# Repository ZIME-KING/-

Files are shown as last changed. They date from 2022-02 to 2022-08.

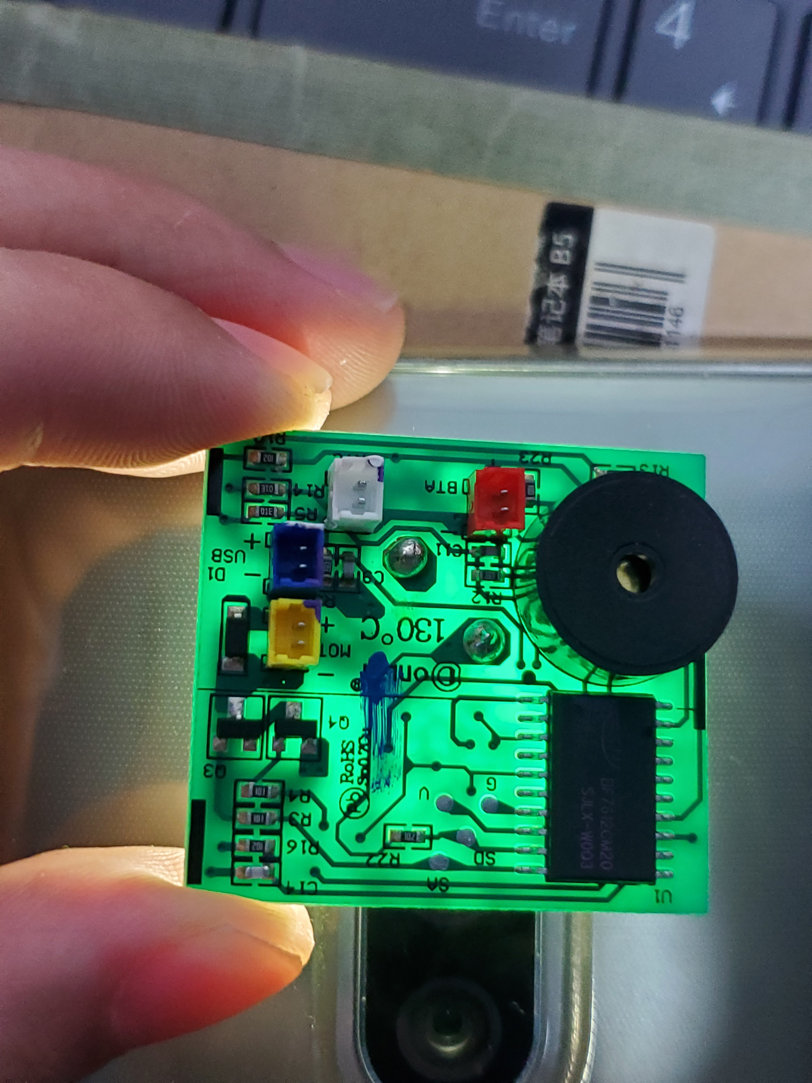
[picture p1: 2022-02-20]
相关资料/362061009228397355.jpg

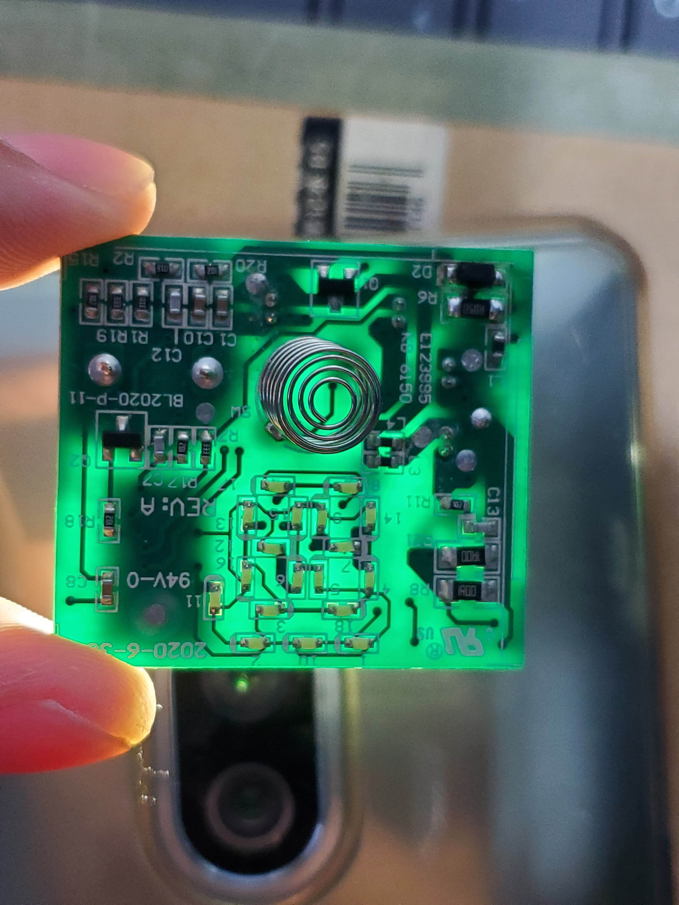
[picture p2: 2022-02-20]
相关资料/814733917850641346.jpg

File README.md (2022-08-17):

# -
搅拌杯项目基于ES7P0693
ES7P0693 http://www.essemi.com/index/product/detail?id=863 工具链软件下载

PCB_03_31 是目前测试使用版本，BOM中NTC分压电阻改为330K
PCB_05_18版新加LDO经测试加不加都一样未启用
使用的led要标称5mA的，使用标称20mA的led会烧芯片切记！！
整理过后删除多余文件
2022/7/3    by: ZL

/////////////////////////////////////////////////////////
PCB_07_21 改进充电时测量电池电量方式，去掉LDO口预定为量产版本
老版本程序已更新停用
新加入 搅拌杯_PCB_07_21_生产资料，文件夹
整理过后删除多余文件
2022/7/30    by: ZL
///////////////////////////////////////////////////////
程序更新，充电时mcu电平为win-0.4（二极管压降），rtc计算电压需要切换到4.6，
解决充电时温度不准的问题
2022/8/15    by: ZL

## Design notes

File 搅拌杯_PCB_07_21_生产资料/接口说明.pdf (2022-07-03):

## 测试点说明

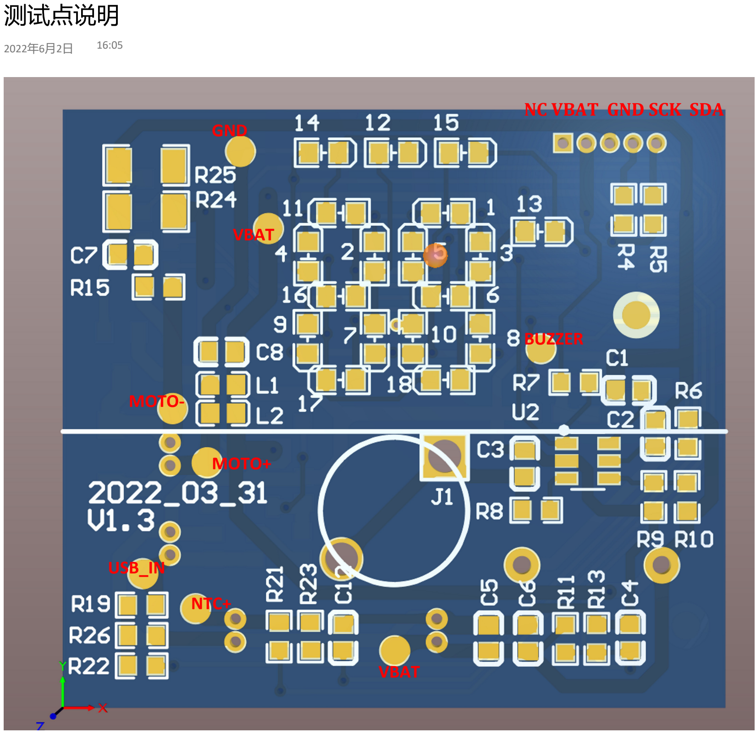
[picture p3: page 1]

GND

NTC+

USB_IN

VBAT

MOTO+

MOTO-

BUZZER

NC VBAT GND SCK SDA

VBAT

2022年6月2日 16:05

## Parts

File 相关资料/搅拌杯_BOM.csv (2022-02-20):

Comment | Description | Designator | Footprint | LibRef | Quantity | 商品编号 | 商品分类 | 名称 | 商品型号 | 品牌 | 封装规格 | 每套数量 | 合计 | 购买数量 | 商品单价 | 金额
FMQ-BUZZER2 |  | BUZZER1 | BUZ-TH_BD12.0-P7.60-D0.6-FD | FMQ-BUZZER2 | 1 | C96079 | 蜂鸣器 | TMB12A12 | TMB12A12 | 华能 | 插件,P=7.6mm | 1 | 1.2205 | 10 | 1.22 | ￥12.21
4.7nF |  | C1 | C0603 | 4.7nF | 1 | C482478 | 贴片电容(MLCC) | 4.7nF ±10% 50V | HGC0603R7472K500NTHJ | Chinocera(华瓷) | 603 | 1 | 0.023748 | 100 | 0.023748 | ￥2.37
0.1u |  | C2, C4, C6, C7, C8, C10, C13, C14 | C0603 | 0.1u | 8 | C141382 | 贴片电容(MLCC) | 100nF ±10% 16V | CT41G-0402-2X1-16V-0.1μF-K(N) | TORCH(火炬) | 603 | 8 | 0.13964 | 100 | 0.017455 | ￥1.75
1uF |  | C3 | C0603 | 1uF | 1 | C908011 | 贴片电容(MLCC) | 1.0uF ±10% | GRM188R71E105KA12J | muRata(村田) | 603 | 1 | 0.189913 | 20 | 0.189913 | ￥3.80
nc |  | C5 | C0603 | nc | 1 |  |  |  |  |  |  | 1 | 0
10uF |  | C9, C11 | C0603 | 10uF | 2 | C669868 | 贴片电容(MLCC) | 10uF ±20％ | JMK107BC6106MA-T | TAIYO YUDEN(太诱) | 603 | 2 | 0.271632 | 20 | 0.135816 | ￥2.72
4.7uF |  | C12 | C0603 | 4.7uF | 1 | C380324 | 贴片电容(MLCC) | 4.7uF ±10% 10V | TCC0603X5R475K100CT | CCTC(三环) | 603 | 1 | 0.04894 | 50 | 0.04894 | ￥2.45
530470210 |  | CN1, CN2, CN3, CN4 | CONN-TH_0530470210 | 530470210 | 4 | C114130 | 线对板/线对线连接器 | 线至板连接器,2P,针座,1.25mm,直插,1排 | 530470210 | MOLEX | 插件,P=1.25mm | 4 | 1.502624 | 40 | 0.375656 | ￥15.03
1N5819HW-7-F |  | D1 | SOD-123_L2.8-W1.8-LS3.7-FD | 1N5819HW-7-F | 1 | C82544 | 肖特基二极管 | 40V 1A 450mV@1A | 1N5819HW-7-F | DIODES(美台) | SOD-123 | 1 | 0.405765 | 10 | 0.405765 | ￥4.06
1N4148W |  | D2 | SOD-123FL_L2.6-W1.6-LS3.4-RD | 1N4148W | 1 | C129216 | 开关二极管 | 75V 150mA 4ns | 1N4148W D1 | TC(德昌) | SOD-123FL | 1 | 0.123717 | 50 | 0.123717 | ￥6.19
HDR-M-2.54_1x1,，弹簧片 |  | J1 | HDR-M-2.54_1X1 | HDR-M-2.54_1x1 | 1 | 触摸弹簧 |  |  |  |  |  | 1 | 0
BEAD |  | L1, L2 ,L3 | L0603 | 22uH | 2 | C2885872 | 贴片电感 | 22uH ±10% | MLI1608F-220KT | Meled(美莱) | 603 | 2 | 0.333902 | 40 | 0.166951 | ￥6.68
LED-0603_W |  | LED1, LED2, LED3, LED4, LED5, LED6, LED7, LED8, LED9, LED10, LED11, LED12, LED13, LED14, LED15, LED16, LED17, LED18, LED19, LED20, LED21 | LED0603-FD_WHITE | LED-0603_W | 21 | C434422 | 发光二极管 | 白光 | SZYY0603W | yongyu(永裕光电) | 603 | 21 | 1.60902 | 250 | 0.07662 | ￥19.16
2N7002 |  | Q1, Q4, Q5 | SOT-23_L2.9-W1.3-P0.95-LS2.4-BR | 2N7002 | 3 | C8545 | 场效应管(MOSFET) | N沟道 60V 115mA | 2N7002 | CJ（江苏长电/长晶） | SOT-23(SOT-23-3) | 3 | 0.469026 | 40 | 0.156342 | ￥6.25
CJ2301 S1 |  | Q2 | SOT-23-3_L3.0-W1.7-P0.95-LS2.9-BR | CJ2301 S1 | 1 | C8547 | 场效应管(MOSFET) | P沟道 20V 2.3A | CJ2301 S1 | CJ（江苏长电/长晶） | SOT-23(SOT-23-3) | 1 | 0.299096 | 10 | 0.299096 | ￥2.99
SS8050 |  | Q3 | SOT-23-3_L2.9-W1.3-P1.90-LS2.4-BR | SS8050 | 1 | C908250 | 三极管(BJT) | NPN 25V 1.5A | SS8050 | FUXINSEMI(富芯森美) | SOT-23 | 1 | 0.098093 | 50 | 0.098093 | ￥4.90
100R |  | R1, R3, R4, R29, R32 | R0603 | 100R | 5 | C105588 | 贴片电阻 | 100Ω ±1% 100mW | RC0603FR-07100RL | YAGEO(国巨) | 603 | 5 | 0.03212 | 200 | 0.006424 | ￥1.28
1K |  | R2, R8, R16, R17, R18, R21, R23, R24, R26, R27, R31, R33 | R0603 | 1K | 12 | C880900 | 贴片电阻 | 1kΩ ±1% 0.1W | SR06X1001FTL | 华新科(Walsin) | 603 | 12 | 0.258924 | 200 | 0.021577 | ￥4.32
10K |  | R6 | R0603 | NC | 1 |  |  |  |  |  |  | 1 | 0
1M |  | R7, R11, R14, R15 | R0603 | 1M | 4 | C22935 | 贴片电阻 | 1MΩ ±1% 1/10W | 0603WAF1004T5E | UNI-ROYAL(厚声) | 603 | 4 | 0.029884 | 100 | 0.007471 | ￥0.75
3M |  | R12, R13 | R0603 | 3M | 2 | C23156 | 贴片电阻 | 3MΩ ±1% 1/10W | 0603WAF3004T5E | UNI-ROYAL(厚声) | 603 | 2 | 0.02072 | 100 | 0.01036 | ￥1.04
0R |  | R20，R5 | R0603 | 0R | 2 | C100044 | 贴片电阻 | 0Ω ±1% 100mW | RC0603FR-070RL | YAGEO(国巨) | 603 | 2 | 0.013334 | 100 | 0.006667 | ￥0.67
0.5R |  | R22 | R1206 | 0.5R | 1 | C168608 | 贴片电阻 | 0.5Ω ±1% | WW12WR500FTL | 华新科(Walsin) | 1206 | 1 | 0.059949 | 50 | 0.059949 | ￥3.00
33K |  | R25, R30 | R0603 | 33K | 2 | C352329 | 贴片电阻 | 33kΩ ±1% 100mW | AECR0603F33K0K9 | RESI(开步睿思） | 603 | 2 | 0.040734 | 100 | 0.020367
1R |  | R34, R35 | R1206 | 1R | 2 | C102295 | 贴片电阻 | 1Ω ±5% 1/4W | CR1206J401R0G | LIZ(丽智电子) | 1206 | 2 | 0.049056 | 100 | 0.024528 | ￥2.45
100K |  | R222, R227 | R0603 | 100K | 2 | C14675 | 贴片电阻 | 100kΩ ±1% 100mW | RC0603FR-07100KL | YAGEO(国巨) | 603 | 2 | 0.013304 | 100 | 0.006652 | ￥0.67
ES7P0693FHTF |  | U1 | TSOP20 | ES7P0693FHTF | 1 |  |  |  |  |  |  | 1 | 0
AS01C(AI01) |  | U2 | SOT-23-6_L2.9-W1.6-P0.95-LS2.8-BL | AS01C(AI01) | 1 | C389617 | 触摸传感器 | AS01C(AI01) | AS01C(AI01) | Sam&wing(芯网) | SOT-23-6 | 1 | 1.3982 | 10 | 1.3982 | ￥13.98
HE4054B |  | U3 | SOT-23-5_L3.0-W1.7-P0.95-LS2.8-BR | HE4054B | 1 | C841234 | 电池管理 | 4054 | LTH7R. | FM富满 | SOT-23-5 | 1 | 0.597374 | 5 | 0.597374 | ￥2.99
 |  |  |  |  |  |  |  |  |  |  |  |  | 9.249215

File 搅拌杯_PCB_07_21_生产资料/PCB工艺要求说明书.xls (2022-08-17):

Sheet: Sheet1
PCB加工工艺要求说明书
文件名： |  | 搅拌杯PCB |  | 版本号： |  | 1 |  | 用途说明： |  | 搅拌杯PCB
PCB加工要求：
加工厂家：
 |  |  |  |  |  |  |  |  |  | 安装位图
合同编号：
 | 1.数 量： |  | 10 | 块
 | 2.层 数：
 | 3.尺 寸： |  | 36 |  | mm | X | 32.5 |  | mm
 | 4.板 厚：
 | 5.材 料： |  |  |  |  | 其他材料：
 | 6.铜箔厚度： |  | 内层 |  |  | 外层
 | 7.阻 焊： |  |  |  | 颜 色：
 | 8.字 符： |  |  |  | 颜 色：
 | 9.测 试：
 | 10.设计软件及其版本：
 | 11.过孔是否塞油：
 | 12.交货日期：
 | 13.过孔是否覆盖阻焊：
 | 14.表面涂层：
 | 15.加工厂商标记：
 | UL标记：
 | 制作日期：
 | 16.交货方式： |  |  |  | 1*1 | 单元/片 |  | 拼板交货允许报废 |  |  | PCS/SET
 | 17.其 他：
 | 18.层次排列： |  | 层的文件名 |  |  |  |  |  |  | 层的说明
 |  |  | 搅拌杯PCB.GTL
 |  |  | 搅拌杯PCB.GBL
其他特殊说明：
公司名称
部 门： |  | 研发部
联系人： |  | 王香连 |  |  |  |  |  | 电话：
电 话： |  | 15000462770 |  |  |  |  |  | 传真：
邮 箱： |  | wangxianglian200@163.com |  |  |  |  |  | 文件初审工程师：

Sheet: Sheet2
无
1张 | 单面 | 0.2mm | H/H oz | H/H oz | 单面 | 绿色 | 白色 | Gerber 文件 | FR-4 | 年周 | 无铅标记 | 有铅喷锡
2张 | 双面 | 0.4mm | 1/1 oz | 1/1 oz | 双面 | 红色 | 黑色 | Protel Dos | FR-4TG170 | 周年 | 防静电 | 无铅喷锡
3张 | 4层 | 0.6mm | 2/2 oz | 2/2 oz | 无 | 蓝色 | 黄色 | PADS 2005 | Rogers 4003 | 年月日 |  | 化学沉金
4张 | 6层 | 0.8mm | 3/3 oz | 3/3 oz |  | 黑色 | 红色 | PADS 2007 | Rogers 4350 | 日月年 |  | OSP(防氧化）
5张 | 8层 | 1.0mm | 4/4 oz | 4/4 oz |  | 白色 | 其它规格 | PADS 2005SP2 | Ro 其它型号 | 其它 |  | 沉锡
6张 | 10层 | 1.2mm | 5/5 oz | 5/5 oz |  | 哑光绿色 |  | Protel 98 | Taconic系列 |  |  | 沉银
7张 | 12层 | 1.5mm | 6/6 oz | 6/6 oz |  | 哑光黑色 |  | Protel 99SE | 铝基材料 |  |  | 其它
8张 | 14层 | 1.6mm | 其它规格 | 其它规格 |  | 哑光蓝色 |  | Protel DXP | 其它
 | 16层 | 2.0mm |  |  |  | 其它规格 |  | PowerPCB 2.1
 | 18层 | 2.5mm |  |  |  |  |  | PowerPCB 4.0
 | 20层 | 3.0mm |  |  |  |  |  | PowerPCB 5.0
 | 其它 | 4.0mm |  |  |  |  |  | 其它格式
 |  | 5.0mm
 |  | 6.0mm
 |  | 其它规格

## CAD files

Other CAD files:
搅拌杯程序/user_code_NEW/HRCC Project Application1/HRCC Project Application1/debug/math_97/math.obj
相关资料/搅拌杯主板图档(1).dwg

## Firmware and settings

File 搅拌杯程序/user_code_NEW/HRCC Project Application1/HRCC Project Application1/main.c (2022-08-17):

/*sample.c*/
#include <hic.h>
#include "main.h"

unsigned long global_count=0;//全局时间计数1ms ++
unsigned char State_flag=1;//运行状态
unsigned int  sleep_count=0;//休眠时间计数
unsigned char buzzer_flag=0;//蜂鸣器启动标记
char temperature;//温度值 0~99
unsigned char Vbat_val;   //电量%  0~99

#define NEW_CODE

unsigned char display_buf[18]={0,0,0,0,0,0,0,0,0,0,0,0,0,0,0,0,0,0};//显示缓存 display_buf[1-1]=1； 1号LED亮
unsigned long Get_Sys_time(){
	return global_count;
}
/******************************************************
函数名：void RAMclear(void)
描  述：RAM区数据清零，RAM区地址0x0000~0x03FF
输入值：无
输出值：无
返回值：无
*******************************************************/
void RAMclear(void){
    for (IAAH=0; IAAH<=0x03; IAAH++)
    {
        for (IAAL=0; IAAL<0xFF; IAAL++)
            IAD = 0x00;
        IAD = 0x00;
    }
}

/**********************************************
函数名：void sleep(void)
描  述：进入IDLE模式
输入值：无
输出值：无
返回值：无
**********************************************/
void sleep(void)
{
    PWRC &= 0x3F;
    PWRC |= 2<<6;        //选择IDLE模式
    __Asm IDLE;     //进入IDLE模式
}

/******************************************************
函数名：void GPIOInit(void)
描  述：首先初始化所有未用到的IO口为输出低电平
输入值：无
输出值：无
返回值：无
*******************************************************/
void GPIOInit(void)
{
    ANSH = 0xFF;        //选择对应端口为数字IO功能
    ANSL = 0xFF;        //选择对应端口为数字IO功能
    PAT  = 0x00;        //所有IO设为输出低电平
    PBT  = 0x00;		
    PCT  = 0x00;
    PA   = 0x00;
    PB   = 0x00;
    PC   = 0x00;
	
	PAT3=0;		//PA3 复用RST脚，设置数字输出
	PAT2=0x01;	//PA2 数字输入 触摸按键
	PBT5=0x01;  //PB5 数字输入
	PB5=1;

	INTC0 |=0x80;       //usb检测双边触发
	PIE7 = 1;           //打开管脚中断
    PIF7 = 0;           //清除外部中断标志

	PAPU=0x00;
	
	//PA3DS：PA3 端口电流选择位
	 //PA1DS=1;	
	 PA3DS=1;
	 PA4DS=1;
	 PA5DS=1;
	 //PB0DS=1;
	 PC1DS=1;
	 //PC0DS=1;

	// 设置AIN11 PB1  MOTO_CUR
	// 设置AIN4  PB2  VBAT
	// 设置AIN9  PB4  NTC
	ANSH3=0;  //PB1/AIN11
	ANSL4=0;  //PB2/AIN4
	ANSH1=0;  //PB4/AIN9
}

void Timer_T8_Init(){
	//16MHZ 时钟 1ms中断
      T8NC = 0x0D;         //定时器模式，预分频1:(Fosc/2)/64
	//  16MHZ 时钟 0.51ms中断
    //T8NC = 0x0C;         //定时器模式，预分频1:(Fosc/2)/32
    //T8NC = 0x0F;         //定时器模式，预分频1:(Fosc/2)/256
	//T8NC = 0x08;         //定时器模式，预分频1:(Foc/2)/2
    T8N = 131;           //赋计数器初值
    T8NIE = 1;           //打开定时器溢出中断
    T8NIF = 0;           //清溢出标志位
    GIE = 1;             //开全局中断
    T8NEN = 1;           //使能T8N
}


void Delay_ms(unsigned int delay){
	static long temp_time;
	temp_time=Get_Sys_time();
	while(Get_Sys_time()-temp_time<delay);
}

void TEST_Delay_ms(unsigned int delay){
	   int i;
	   for(i = 0;i<500*delay;i++);        //延时
}

/******************************************************
函数名：void Timer_T21_Init(void)
描  述：定时器T21初始化
*******************************************************/
void Timer_T21_Init(){
	unsigned int ch0_duty=500;
	unsigned int ch1_duty=500;
	T21CL = 0xC0;        //多精度pwm模式
    T21CM = 0x3F;        //T21_CH0输出低有效、T21_CH1输出低有效，预分频1:16
   // T21OC = 0x45;        //T21_CH0，T21_CH1,开启在PA0，PA7上，PWM时钟源选择INTHRC
    T21OC = 0x41;        //T21_CH0,开启在PA0，PWM时钟源选择INTHRC
   

    T21PH = 4000 >> 8;        //pwm周期
    T21PL = 4000 & 0xFF;

	ch0_duty=4000;
//	ch1_duty=4000;

    T21R0H = ch0_duty >>8 ;       //pwm0占空比
    T21R0L = ch0_duty & 0xFF;

//    T21R1H = ch1_duty >>8;		//pwm1占空比
//   T21R1L = ch1_duty & 0xFF;
    
	T21TR = 1;           //启动pwm输出
    T21PIE = 1;          //打开T21周期2中断    
    T21PIF = 0;          //清标志位
    GIE = 1;             //开全局中断    
    T21EN = 1;           //使能T21
}

void Timer_T31_Init(){
    T31C2L = 0x00;      //禁止从模式，使用内部HRC(16mHz)作为计数器时钟源
    T31C0L = 0x00;      //T31CNTLD寄存器无缓冲，写入值立即生效。计数器边沿计数模式，向上计数
    T31CNTLDH = 0x00;     //重装载值，计数器与其匹配时产生事件
    T31CNTLDL = 0x3E;
    T31PRSH = 0x00;       //预分频系数1:16
    T31PRSL = 0x0F;
    T31POS = 0x0F;        //计数器与T31CNTLD第16次匹配事件时产生溢出中断  
    UPIE = 1;       //打开计数溢出中断
    T31IE = 1;      //开启多功能定时器中断
    UPIC = 1;       //清溢出标志位
    T31IF = 0;      //清定时器总标志位
    GIE = 1;        //开启全局中断
    T31EN = 1;      //使能计数器
}

//
//输入值为0~999
//
void Set_PWM_CH0_Duty(int duty){
	    T21R0H = duty >>8 ;     //pwm0占空比
		T21R0L = duty & 0xFF;
}
void Set_PWM_CH1_Duty(int duty){
		T21R1H = duty >>8;		//pwm1占空比
		T21R1L = duty & 0xFF;
}
//#define BUZER_N  //无源
#define BUZER_A	 //有源
#ifdef BUZER_N
unsigned char Buzzer_Init(void){
	BEEPC=0xD8;
	return 0xff;
}
void Buzzer_Stop(){
	BEEPEN=0;
}
void Buzzer_Start(){
	BEEPEN=1;
}
#endif

#ifdef BUZER_A
unsigned char  Buzzer_Init(void){
	return 0x88;
}
void Buzzer_Stop(){
	PB7=0;
}
void Buzzer_Start(){
	PB7=1;
}
#endif

void State_Trans(unsigned char new_state){
	State_flag=new_state;
}
unsigned char Get_State(){
	return State_flag;
}
void Buzzer_Task(){
	if(Get_State()!=3){
		if(buzzer_flag){
			Buzzer_Start();
			buzzer_flag=0;
		}
	else{
		Buzzer_Stop();
	}
	}
}
unsigned char USB_Check(){
	return PB5;
}
void Sleep_Tsak(){
static unsigned char last_state;
	if(last_state!=Get_State()){
		last_state=Get_State();
		sleep_count=0;
	}
	  sleep_count++;
	if(Get_State()==1){
		if(sleep_count>180){
			State_Trans(0);
		}
	}
	else if(Get_State()==2){
		if(sleep_count>120){
			State_Trans(0);
		}
	}
	else if(Get_State()==3){
		if(sleep_count>3){
			State_Trans(0);
			//sleep();
		}
	}
}

void LED_Task(){
//显示温度
	//char temp;
	//RV;vcc_val
	//temp=vcc_val*10;
	//D1_NUM(temp /10);
	//D2_NUM(temp %10);
	display_buf[13-1]=1;

	if(temperature==0xff){
	  //D1_NUM(0xff);
	  //D2_NUM(0xff);	
	  D1_NUM(8);
	  D2_NUM(8);	
	}
	else{
	  D1_NUM(temperature/10);
	  D2_NUM(temperature%10);	
	}

	//D1_NUM(Vbat_val/10);
	//D2_NUM(Vbat_val%10);


	//vcc_val
//电量指示
	if(USB_Check()){
		if(0<=Vbat_val && Vbat_val<30){
			display_buf[14-1]=!display_buf[14-1]; //左一闪
			display_buf[12-1]=0; 
			display_buf[15-1]=0;
		}
		else if(30<=Vbat_val && Vbat_val<60){
			display_buf[14-1]=1;
			display_buf[12-1]=!display_buf[12-1]; //左一亮 左二闪
			display_buf[15-1]=0;
		}
		else if(60<=Vbat_val && Vbat_val<90){
			display_buf[14-1]=1;
			display_buf[12-1]=1; 
			display_buf[15-1]=!display_buf[15-1]; //左一亮 左二亮 左三闪
		}
		else if(90<=Vbat_val){
			display_buf[14-1]=1;
			display_buf[12-1]=1; 
			display_buf[15-1]=1; //左一亮 左二亮 左三亮		
		}
	}
	else{
		if(0<=Vbat_val && Vbat_val<33){
			display_buf[14-1]=1;
			display_buf[12-1]=0; 
			display_buf[15-1]=0; //左一亮 左二亮 左三亮				
		}
		else if(33<=Vbat_val && Vbat_val<66){
			display_buf[14-1]=1;
			display_buf[12-1]=1; 
			display_buf[15-1]=0; //左一亮 左二亮 左三亮		
		}
		else if(66<=Vbat_val && Vbat_val<=99){
			display_buf[14-1]=1;
			display_buf[12-1]=1; 
			display_buf[15-1]=1; //左一亮 左二亮 左三亮		
		}
	}	
	Updata_SCAN_LED_BUF_L();
}
//进入休眠状态
void state_0(){
	//PA1=0;
	//Buzzer_Stop();
	//unsigned char str[]="aaa";
	//UART_send(str,1,1);
	Delay_ms(20);
	buzzer_flag=0;
	char i;
	i=18;
	while(i--)
	display_buf[i]=0;
	Updata_SCAN_LED_BUF_L();
	//LED_Clear();
	//Set_PWM_CH0_Duty(999);
	//Set_PWM_CH1_Duty(999);
	Timer_T21_Init();
	//RAMclear();
	 State_Trans(3);
	//配置PA2中断模式唤醒
	
	ANSL = 0xFF;        //选择对应端口为数字IO功能
	ANSH = 0xFF;
    PAT = 0x00;         //所有IO设为输出低电平
    PBT = 0x00;
    PCT = 0x00;
    PA = 0x00;
    PB = 0x00;
    PC = 0x00;

	PAT2=0x01;	//PA2 数字输入
	KIE=1;
	KMSK1=1;
	PAPU=PAPU|0X04;

	PBT5=0x01;  //PB5 数字输入
	PB5=1;

	INTC0 |=0x80;       //usb检测双边触发
	PIE7 = 1;           //打开管脚中断
    PIF7 = 0;           //清除外部中断标志

	ADC_dis_init();
	sleep();
}
//全关检测按键长按开机
void state_3(){

	unsigned char i=18;
	while(i--)
	display_buf[i]=0;
	Updata_SCAN_LED_BUF_L();
	LED_Clear();
	T8NEN = 0;           //使能T8N
}

//电机关 开灯
void state_1(){
	Set_PWM_CH0_Duty(4000);
	//Set_PWM_CH1_Duty(4000);
}

//电机开
void state_2(){
	//Set_PWM_CH1_Duty(0);
	Set_PWM_CH0_Duty(400);
}
void State_Ruun(){
			switch (State_flag){
				case 3:
					state_3();
				break;
				case 1:
					state_1();
				break;
				case 2:
					state_2();
				break;
				case 0:
					state_0();
				break;
			}
}


void user_delay(){
unsigned int i=4000;
while(i--);
}


void main(void) 
{
	//RAMclear();
	WDTC = 0x16;         //分频比1:128，使能WDT预分频器，看门狗溢出时间t=256*128/32000=1.024s

	SetTime();			//任务间隔时间初始化
	GPIOInit();
	Timer_T8_Init();
	Timer_T21_Init();
	ADC_init() ;
	Buzzer_Init();
	LED_Clear();
	PB3=1;
//    Uart_Init();
#ifdef UART_TEST
	Uart_Init();
#endif

	int iii=110;
	while(iii--){
		user_delay();
		//user_delay();
		User_Get_measure_Val();
	}
	if(Vbat_val==0 && USB_Check()==0){
		 state_0();
		//sleep();
		//__Asm RST;
	}
	
	Timer_T31_Init();
	LED_Task();
	buzzer_flag=1;

	while (1)
    {
		if(CompareTime(&Task_10)){
			GetTime(&Task_10);
			//User_Get_measure_Val_10ms();	
		}

	  if(CompareTime(&Task_50)){
			GetTime(&Task_50);
			Buzzer_Task();
			if(touch_key_busy){
			touch_key_busy=0;
			sleep_count=0;
				if(touch_key_staus==SHORT ){
						if(Get_State()==2) {
							State_Trans(0);
							//state_0();
							//sleep();
						}
				}
				if(touch_key_staus==DOUBLE){
						if(Get_State()==1 && USB_Check()==0){
							State_Trans(2);
						}
				}
				if(touch_key_staus==LONG_NO_RELEASE){
						if(Get_State()==3) 
						{
							__Asm RST;     //
						}//State_Trans(1);
				}
			}
	  }
	  if(CompareTime(&Task_100)){
		  GetTime(&Task_100);

		  User_Get_measure_Val_10ms();

		  User_Get_measure_Val();		//ADC测量



		  State_Ruun();					//状态运行

		  #ifdef UART_TEST
		    unsigned char str[]="状态 的转换值为:    \r\n\0";
		    unsigned char str1[]="声音 的转换值为:    \r\n\0";

			//GIE=0;
			//UART_send(str,1,State_flag);
			//UART_send(str1,1,buzzer_flag);
			//GIE=1;
		#endif

		  if(USB_Check()==1){
			 State_Trans(1);
			 sleep_count=0;
		  }
	  }
	  if(CompareTime(&Task_1000)){
		  GetTime(&Task_1000);
		  // unsigned char str[]="状态 的转换值为:    \r\n\0";
		  //UART_send(str,1,State_flag);

			Sleep_Tsak();
			if(Get_State()!=3){
				LED_Task();
			}

	  }
		//if(Get_State()==3){
			//unsigned char i=18;
			//while(i--)
			//display_buf[i]=0;
			//Updata_SCAN_LED_BUF_R();
			//LED_Clear();
		//}
        CLRWDT();
    }
}

/*******************************************************
函数名：void isr(void) interrupt
描  述：中断服务程序
输入值：无
输出值：无
返回值：无
*******************************************************/
//unsigned int timer_cnt;
 unsigned char cnt_0;
void isr(void) interrupt
{
    if (T8NIE==1 && T8NIF==1)        //定时器溢出中断
    {
        T8NIF = 0;        //清标志位
        T8N += 131;       //进中断先赋计数器初值
		SCAN_NEW();       //刷新LED
    }
	  if (T21PIE==1 && T21PIF==1)        //定时器pwm周期中断
    {
        T21PIF = 0;                //清标志位
    }

	if (UPIS==1 && UPIF==1)        //定时器溢出中断
    {
        UPIC = 1;       //清溢出标志位，UPIF必须要在T31IF之前清除
        T31IF = 0;      //清定时器总标志位，UPIF必须要在T31IF之前清除
		//PB3=~PB3;
		global_count++;
		scan_touch_key();
    }


	    if(KIF==1 && KIE==1)
    {
		PA2=1;
		KIF = 0;       //清中断标志位
    }
	    if(PIE7==1 && PIF7==1) //usb插入
    {
		sleep_count=0;
		if(State_flag==2 )State_flag=1;    
		
        
		if(State_flag==3){
			__Asm RST;     //
		}

		
		PIF7 = 0;		 //清除外部中断
    }
}

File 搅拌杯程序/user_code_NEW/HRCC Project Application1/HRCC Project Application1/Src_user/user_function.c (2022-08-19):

#include "../main.h"
#include "../inc_user/user_function.h"
#include <math.h>
//#include <stdlib.h>



/*********************************************************
*Copyright (C), 2020, Shanghai Eastsoft Microelectronics Co., Ltd
*文件名:  adc_offset.c
*作  者:  AE Team
*版  本:  v1.0，编译于iDesigner(v4.2.3.166) + 工具链HRCC(v1.2.0.106)
*日  期:  2020/12/25
*描  述:  ADC通信演示
          PA7：模拟输入端口
          PB5：TX
          PB6：RX 
          程序将转换完的AD值通过串口发送到上位机，波特率9600bps。宏定义VDDVREF选择VDD作为参考电压正端，
          否则选择内部2.048V作为参考电压正端。
		  转换值减去offset进行ADC软件补偿，offset为802FH（内部2.048V作参考）和8030H（VDD作参考）低8位数据，
		  IAP读16位数据后需先判断是否满足高低8位取反。
		  注意：由于offset的存在，为防止溢出，转换值小于offset时，ADC结果直接归0；并且ADC最大只能测到(0xFFF-offset)。
*备  注:  本软件仅供学习和演示使用，对用户直接引用代码所带来的风险或后果不承担任何法律责任。
**********************************************************/

//#define VDDVREF        //宏定义选择VDD作为参考电压，注释本句则选择内部2.048V作为参考电压正端
//typedef unsigned char uchar;
//typedef unsigned int uint;

uint adc_value;
uint offset_value = 0;  //保存ADC校准值
uchar str[] = "通道 的转换值为:    \r\n\0";


#define B 3950.0//温度系数
#define TN 298.15//额定温度(绝对温度加常温:273.15+25)
#define RN 100// 额定阻值(绝对温度时的电阻值100k)
#define RES 330// 分压电阻200K/330k
#define BaseVol  2.048 //ADC基准电压

float vcc_val;
float temp_vcc_val;
float RV,RT,Tmp;
float Get_Tempture(unsigned int adc)
{        //float RV,RT,Tmp;
        RV=BaseVol*(float)adc/4096.0;		//ADC为12位ADC,求出NTC电压:RV=ADCValu/4096*BaseVoltag
       // RT=RV*100/(BaseVol-RV);				//求出当前温度阻值 (BaseVoltage-RV)/R16=RV/RT;
		RT=RES/((temp_vcc_val/RV)-1);
	    Tmp=1/(1/TN+(log(RT/RN)/B))-273.15;//%RT = RN exp*B(1/T-1/TN)%

        return Tmp;
}
//————————————————
//版权声明：本文为CSDN博主「LVGRAPE」的原创文章，遵循CC 4.0 BY-SA版权协议，转载请附上原文出处链接及本声明。
//原文链接：https://blog.csdn.net/u013866683/article/details/79391849



/**********************************************
函数名：UART_send(uchar *str,uchar ch,uint value)
描  述：UART发送函数
输入值：字符串指针，通道数，ADC转换值
输出值：无
返回值：无
**********************************************/
void UART_send(uchar *str,uchar ch,uint value)
{
    *(str+4) = ch+'0';
    *(str+16) = value/1000+'0';
    *(str+17) = value%1000/100+'0';
    *(str+18) = value%100/10+'0';
    *(str+19) = value%10+'0';

    while(*str)
    {
        while(!TRMT1);
        TX1B = *str++;
    }
}

/**********************************************
函数名：ADC_convert(uchar ch)
描  述：ADC转换函数
输入值：转换通道ch
输出值：无
返回值：转换的12位结果
**********************************************/
uint ADC_convert(void)
{
    ADTRG = 1;      //启动AD转换
    while(ADTRG);
    ADIF = 0;

    return (uint)ADCRH<<8 | ADCRL;
}

/*******************************************************
函数名：uint GetOffset2048(void)
描  述：获取参考电压为内部2.048V时offset值
输入值：无
输出值：无
返回值：offset值
*******************************************************/
uint GetOffset2048(void)
{
	uint value_tmp = 0;
	unsigned char gie_bk = GIE;		//备份GIE

    CLRWDT();

	while(GIE) GIE = 0;
	DATARDEN = 1;

	FRAH = 0x802F >> 8;
	FRAL = 0x802F;
	DATARDTRG = 1;
	while(DATARDTRG) ;	     //等待读完成
	__Asm TBR;		         //查表读指令
	value_tmp = (ROMDH<<8) | ROMDL;

    ROMCL = 0x00;            //退出IAP
	GIE = gie_bk;            //恢复全局中断

	return value_tmp;
}

/*******************************************************
函数名：uint GetOffsetVDD(void)
描  述：获取参考电压为VDD时offset值
输入值：无
输出值：无
返回值：offset值
*******************************************************/
uint GetOffsetVDD(void)
{
	uint value_tmp = 0;
	unsigned char gie_bk = GIE;		//备份GIE

    CLRWDT();

	while(GIE) GIE = 0;
	DATARDEN = 1;

	FRAH = 0x8030 >> 8;
	FRAL = 0x8030;
	DATARDTRG = 1;
	while(DATARDTRG) ;	     //等待读完成
	__Asm TBR;		         //查表读指令
	value_tmp = (ROMDH<<8) | ROMDL;

    ROMCL = 0x00;            //退出IAP
	GIE = gie_bk;            //恢复全局中断

    return value_tmp;
}

/****************初始化UART*******************/
void Uart_Init(void){
    PCT1 = 0;       //TX输出
    PAT5 = 1;       //RX输入
   // PBT5 = 0;       //TX输出
   // PBT6 = 1;       //RX输入
    TX1LEN = 0;     //8位数据发送格式 UART1SEL
    BRGH1 = 0;      //波特率低速模式：波特率=Fosc/(64*(BRR<7:0>+1))
    BR1R = 25;      //波特率=16MHz/(64*26)≈9600bps
    TX1EN = 1;       //打开发送
	UART1SEL=1;
}

void ADC_dis_init(){
  
    ANSH1 = 0;          //选择AIN9为模拟口
    ADCCL = 0xF8;      //ADCCL<7:4>选择通道
	//ADCCL &= 0x9F;      //选择通道9
	//ADCCM = 0x6B;       //参考源内部固定选择2.048V,负参考固定选择VSS，转换位数固定选择12位，AD调整offset固定选择档位1
    ADCCH = 0xC3 ;       //低位对齐;时钟周期FOSC/16
	ADEN = 0;           //使能ADC模块
    VREFEN = 0;         //参考电压模块使能
//	while(j--);         //等待300us以上
	VREF_CHOPEN = 0 ;    //内部参考必须使能电压斩波器
//    while(i--);         //等待1ms以上再启动转换

	ADC_LP_EN = 0;      //ADC低功耗必须固定使能
	PBT4 = 0;
	PBT2 = 0;
    SMPS = 1;           //硬件控制采样，ADTRG=1时启动AD采样转换
}


/**********************************************
函数名：ADC_init()
描  述：初始化ADC
输入值：无
输出值：无
返回值：无
**********************************************/
void ADC_init(void) 
{
    uint j = 3000;        //延时变量
	uint i = 10000;       //延时变量
	uchar cnt = 3;
     
/****************初始化ADC********************/
#ifdef VDDVREF
	while(cnt != 0)
	{
        offset_value = GetOffsetVDD();  //获取offset值
		if((offset_value>>8) == ((~offset_value) & 0x00FF)) //是否满足高低8位取反，是则取低8位作为offset
		{
			offset_value =  offset_value & 0x00FF;

			break;
		}
		else
		{
		    cnt--;

			if(cnt == 0)
			    offset_value = 0;  //读IAP超过3次后仍不满足高低8位取反则offset固定为0
		}
	}
    ANSL7 = 0;          //选择AIN7为模拟口
    ADCCL |= 0xF0;      //ADCCL<7:4>选择通道
    ADCCL &= 0x7F;      //选择通道7
	ADCCM = 0x4B;       //参考源VDD,负参考固定选择VSS，转换位数固定选择12位，AD调整offset固定选择档位1
    ADCCH = 0xC8;       //低位对齐;时钟周期FOSC/16
	ADEN = 1;           //使能ADC模块
#else
	while(cnt != 0)
	{
        offset_value = GetOffset2048();  //获取offset值
		if((offset_value>>8) == ((~offset_value) & 0x00FF)) //是否满足高低八位取反，是则取低8位作为offset
		{
			offset_value =  offset_value & 0x00FF;

			break;
		}
		else
		{
		    cnt--;

			if(cnt == 0)
			    offset_value = 0;    //读IAP超过3次后仍不满足高低8位取反则offset固定为0
		}
	}
    ANSH1 = 0;          //选择AIN9为模拟口
    ADCCL |= 0xF0;      //ADCCL<7:4>选择通道
    ADCCL &= 0x9F;      //选择通道9

	ADCCM = 0x6B;       //参考源内部固定选择2.048V,负参考固定选择VSS，转换位数固定选择12位，AD调整offset固定选择档位1
    ADCCH = 0xC8;       //低位对齐;时钟周期FOSC/16
	ADEN = 1;           //使能ADC模块
    VREFEN = 1;         //参考电压模块使能
	while(j--);         //等待300us以上
	VREF_CHOPEN = 1;    //内部参考必须使能电压斩波器
    while(i--);         //等待1ms以上再启动转换
#endif
	ADC_LP_EN = 1;      //ADC低功耗必须固定使能
	PBT4 = 1;
	PBT2 = 1;
    SMPS = 1;           //硬件控制采样，ADTRG=1时启动AD采样转换
}

void _f(int a[],char len)
{
    //int a[10];
	int n;  //存放数组a中元素的个数
    int i;  //比较的轮数
    int j;  //每轮比较的次数
    int buf;  //交换数据时用于存放中间数据
   // n = sizeof(a) / sizeof(a[0]);  /*a[0]是int型, 占4字节, 所以总的字节数除以4等于元素的个数*/
   //int ii;
    //for(ii=0;ii<len;ii++){
	//	a[ii] = *(num+ii);
	//}
	n=len;
	for (i=0; i<n-1; ++i)  //比较n-1轮
    {
        for (j=0; j<n-1-i; ++j)  //每轮比较n-1-i次,
        {
            if (a[j] < a[j+1])
            {
                buf = a[j];
                a[j] = a[j+1];
                a[j+1] = buf;
            }
        }
    }
    //for(int x=0;x<10;x++)
        //printf("%d\x20", a[x]);
}
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

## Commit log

2022-02-20 提交初始版本
    [math.obj, 搅拌杯.PrjPcb, 搅拌杯PCB.PcbDoc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]
2022-02-20 添加注释
    [math.obj]
2022-02-21 PCB更新V1.1更新丝印，原理图更新
    [搅拌杯PCB.PcbDoc, 搅拌杯原理图.schdoc]
2022-03-04 PCB 更新添加测试点
    [搅拌杯.PrjPcb, 搅拌杯PCB.PcbDoc, 搅拌杯PCB.PcbLib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]
2022-03-06 更新PCB，终
    [搅拌杯PCB.PcbDoc]
2022-03-09 修复sleep问题，ADC初始化后Sleep无效，休眠前需要ADC反初始化
    [math.obj, 搅拌杯PCB.PcbDoc, 搅拌杯原理图.schdoc]
2022-03-10 bug修复
    [math.obj]
2022-03-15 灯单个刷新，亮度均匀
    [math.obj]
2022-03-22 更新程序，添加t3定时器，T8N只做LED扫描，解决唤醒时有闪烁的问题，增加adc采样次数，增加稳定性
    [math.obj, 搅拌杯原理图.schdoc]
2022-04-06 更新PCB，切换LED_IO_加大电流，对应程序也更新了
    [PCB工艺要求说明书.xls, math.obj, 搅拌杯.PrjPcb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]
2022-05-17 资料更新
    [搅拌杯PCB.PcbLib, 搅拌杯原理图.schdoc]
2022-07-03 整理更新
    [PCB工艺要求说明书.xls, math.obj, 搅拌杯.PrjPcb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]
2022-07-29 pcb更新，代码更新电量测量方式更新
    [Bill of Materials-搅拌杯PCB.csv, Pick Place for 搅拌杯PCB.csv, math.obj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]
2022-07-29 更新见readme
    [Bill of Materials-搅拌杯PCB.csv, PCB工艺要求说明书.xls, Pick Place for 搅拌杯PCB.csv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]
